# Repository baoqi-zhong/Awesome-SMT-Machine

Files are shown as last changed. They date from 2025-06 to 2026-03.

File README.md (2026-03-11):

# :fire: Awesome :fire: SMT Machine


[中文文档](./README_CN.md)

Contributors:
<p float="left">
  
  
</p>

**Awesome SMT Machine** is an open-source Pick and Place machine project that originated from an embedded system course. The project features a fully self-developed software, hardware, and mechanical design.

It utilizes a **CoreXY** architecture for 4-DOF placement and integrates a custom **FOC (Field Oriented Control) closed-loop stepper motor driver** for high-precision and high-response positioning. The system includes a 4.2-inch color touch screen for real-time status monitoring and uses Python-based host software for coordinate file parsing and fully automatic placement.

<p float="left">
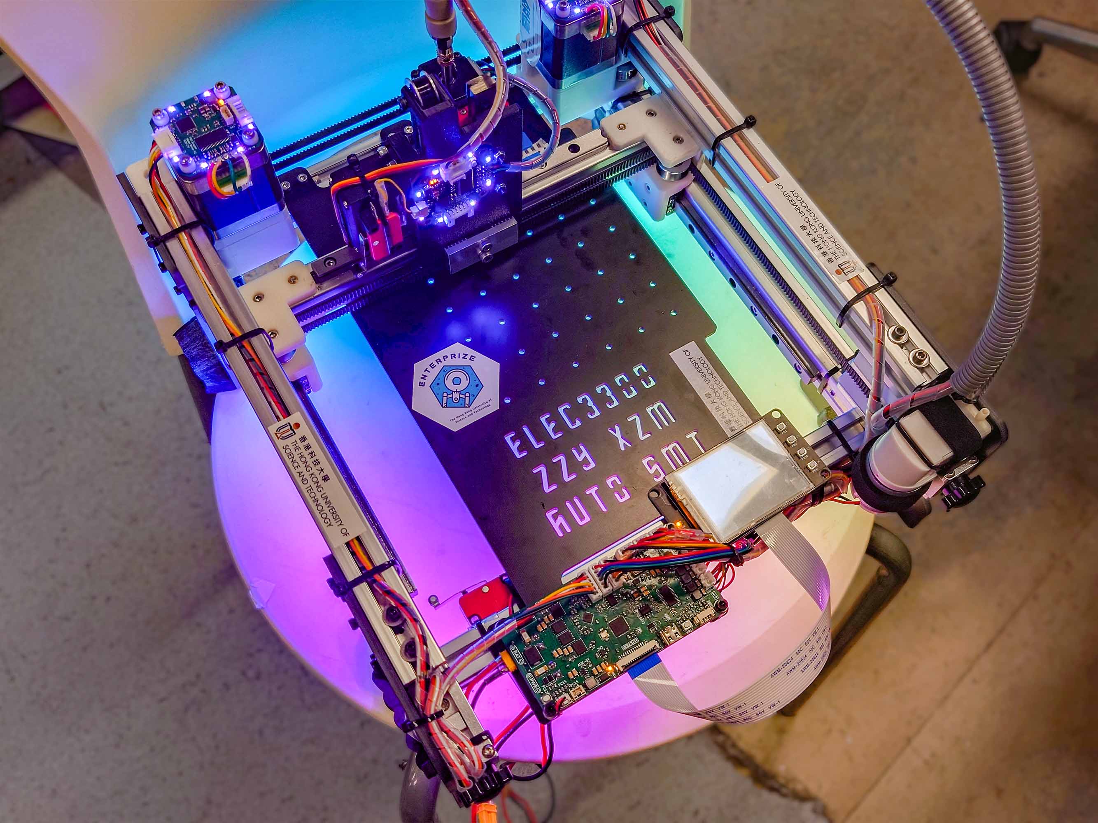
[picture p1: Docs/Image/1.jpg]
  
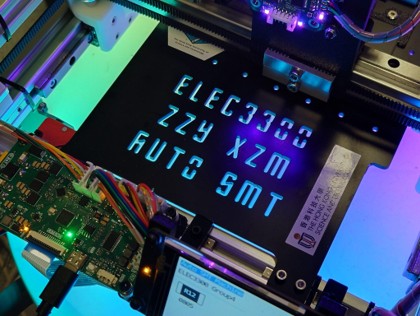
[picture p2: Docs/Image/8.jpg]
  
</p>

**Key Features**:
- **Core-XY Structure**: High precision and high-speed motion.
- **FOC Stepper Driver**: Heat-free, highly efficient, and silent operation.
- **Interactive UI**: 4.2-inch color touch screen.
- **Host Software**: Python-based control for automated workflow.

# Hardware
<p float="left">
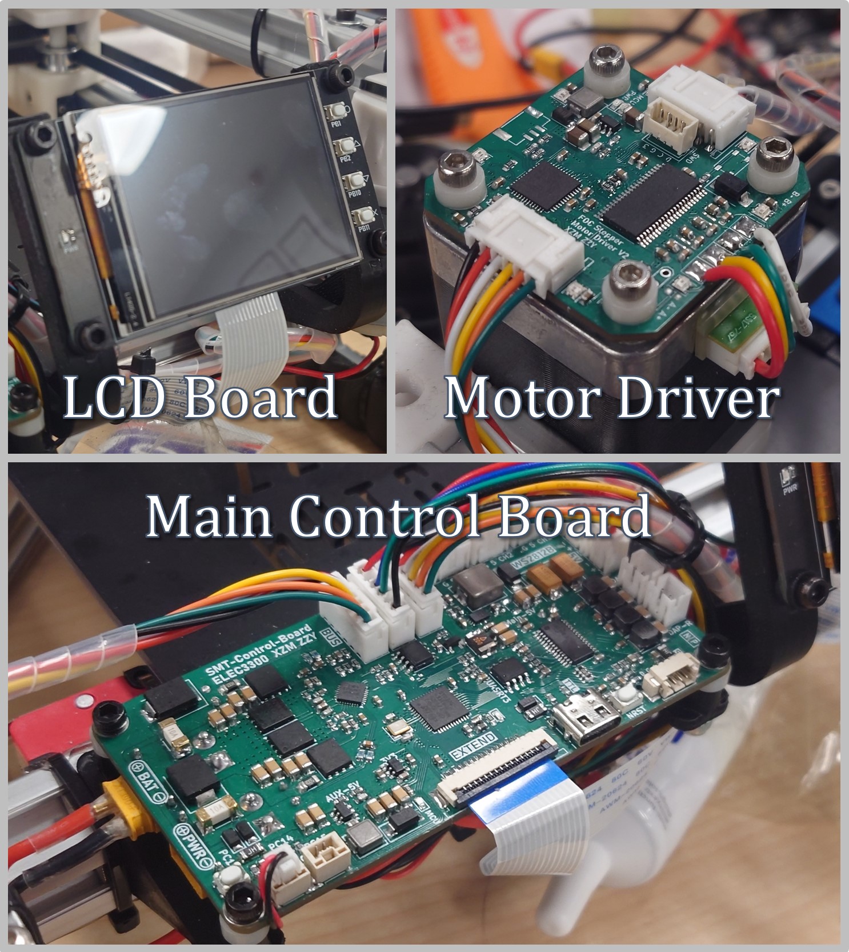
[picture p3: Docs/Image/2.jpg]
  
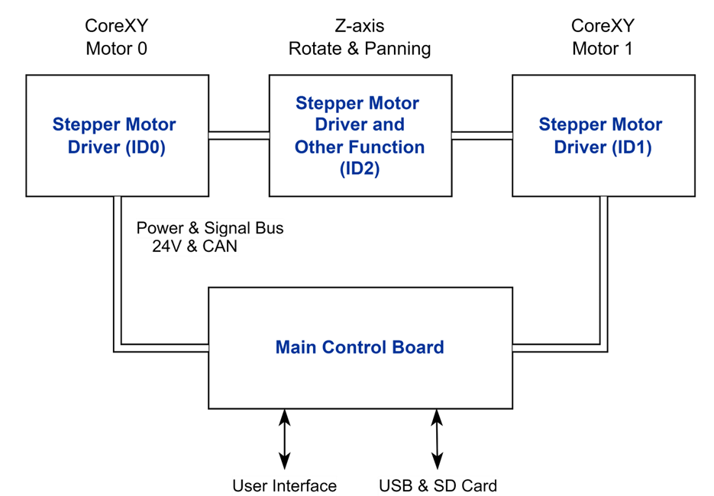
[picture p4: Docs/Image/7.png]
  
</p>

The hardware consists of 4-layer PCBs designed using **KiCad**.

**Directory Structure**:
```
./Hardware/
    Main-Control-Board          Main control motherboard
    Stepper-Motor-FOC-Driver    FOC driver for Nema-17 stepper motors
    LCD-Board                   TFT display interface board
    Dual-Head-Motor-Driver      (Ongoing) Controller for the dual-head placement module
```

## Main Control Board
<p float="left">
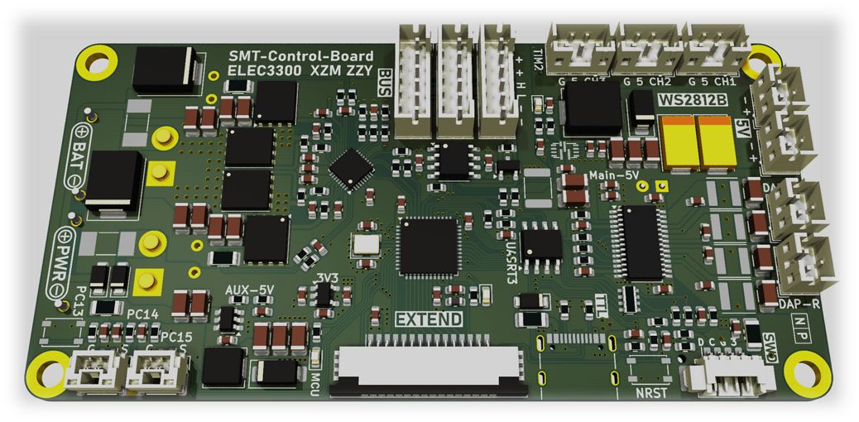
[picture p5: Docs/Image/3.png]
  
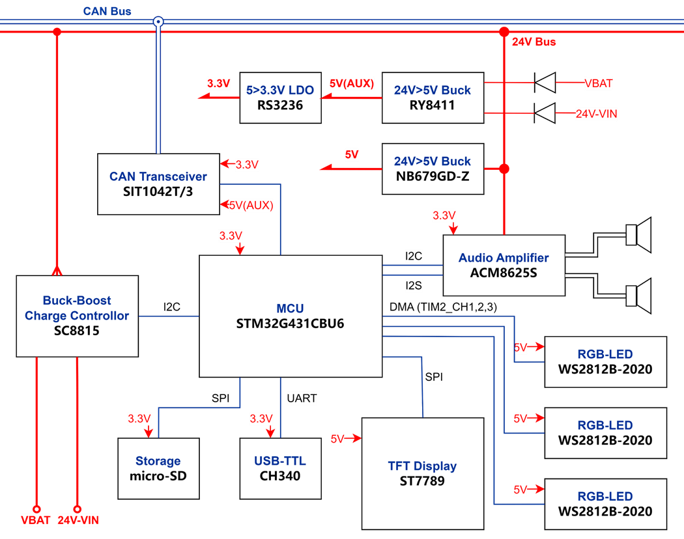
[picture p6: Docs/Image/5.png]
  
</p>

Powered by an **STM32G431CBU6** MCU, SC8815 battery management system, and ACM8625S I2S audio amplifier.  
For details, see [Main Control Board Schematic](./Hardware/Main-Control-Board/Main-Control-Board-Schematic.pdf).

**Features**:
- **UART Interface**: Communication with the Python host software.
- **6S Battery Charger**: Supports fast charging and wide input voltage range.
- **Audio System**: Integrated amplifier and speaker (just for fun! :yum:).
- **CAN Bus**: High reliability and scalability.

## Stepper Motor FOC Driver
<p float="left">
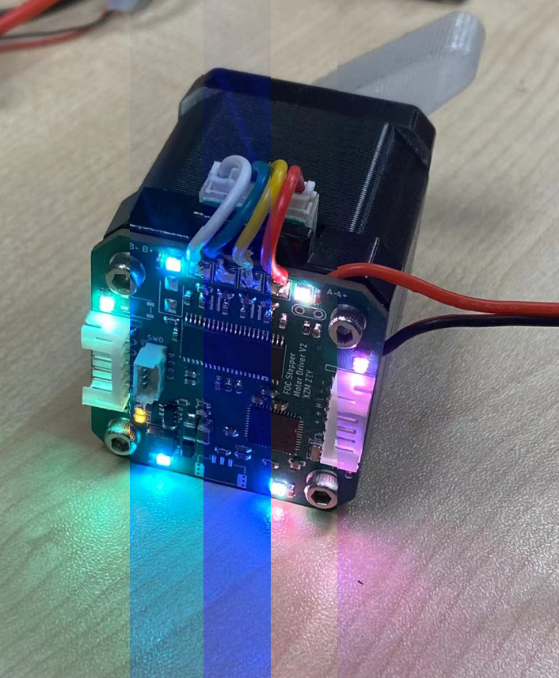
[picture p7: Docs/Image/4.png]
  
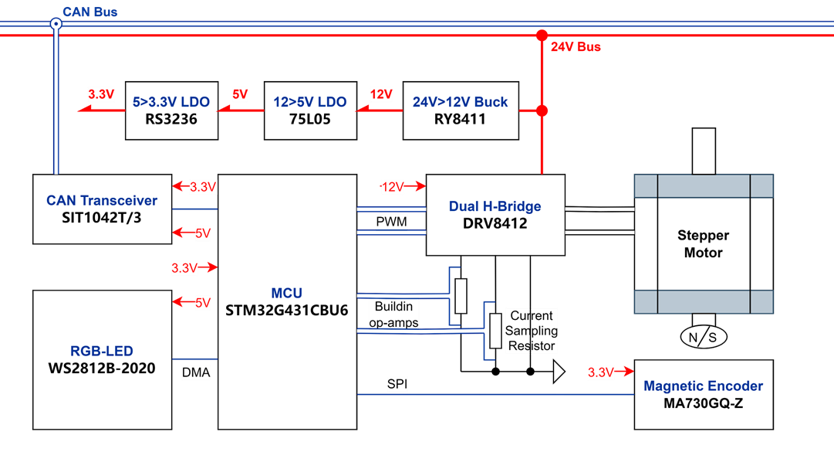
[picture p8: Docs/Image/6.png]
  
</p>

Based on **STM32G431CBU6** MCU, DRV8412 gate driver, MA732 magnetic encoder, and WS2812 RGB LEDs.  
For details, see [Stepper Motor FOC Driver Schematic](./Hardware/Stepper-Motor-FOC-Driver/Stepper-Motor-FOC-Driver-Schematic.pdf).

**Features**:
- **Custom FOC Algorithm**: Three-loop control (Torque, Speed, Angle). Implements DQ-axis decoupling, BEMF feedforward, cogging torque compensation, and dead-time compensation.
- **Precision Control**: Real current loop ensures precise torque control.
- **14-Bit Encoder**: High-speed magnetic encoder with automatic calibration and adaptive notch filter (ANF) for low noise.
- **CAN Bus**: Bi-directional communication.

# Software
The embedded software is developed using **STM32CubeMX**, **Makefile**, and **GCC**. The FOC algorithm is implemented with a bare-metal interrupt-driven architecture for maximum performance. The main control board utilizes **FreeRTOS** for multitasking (communication, motion control, battery management, audio playback, etc.).

**Directory Structure**:
```
./Software/
    ClosePnP                        Python/tkinter-based host control software (inspired by OpenPnP)
    Main-Control-Board-Software     STM32 firmware for the main board
    Stepper-Motor-Driver-Software   FOC algorithm source code
    MusicConverter                  Python script to convert .WAV files to C arrays for audio testing
    Dual-Head-Motor-Driver-Software (Ongoing) Firmware for the dual-head motor driver
```

# Mechanical
The original single-head version was designed using **Cinema 4D (C4D)**. The newer dual-head version is designed with **SolidWorks**.

- **Single-head source files**: `./Mechanical/CoreXY.c4d` (or `./Mechanical/CoreXY.stl`).

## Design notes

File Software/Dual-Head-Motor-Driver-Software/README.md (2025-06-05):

# Dual-Head-Motor-Driver

与电机 FOC 驱动一脉相承. 

## 板上资源
- 三个步进电机的三个全桥驱动
- 三个电机 A 相电流采样(AB 相不共用对地电阻), 以及内部 PGA 运放
- 电机驱动 nFAULT 状态输出
- 输入电压采样
- FDCAN
- GPIO 控制的阀

## TIM 和 ADC: 驱动波形产生与电流采样时机
我们有三个电机, 一共 12 个 timer channel 需要控制, 我们希望他们全部中心对齐. 全部采用中心对齐模式.
对应关系如下:
|相线|Timer & Channel|
|:--|:--|
|M1 A+|TIM3_CH1|
|M1 A-|TIM1_CH1|
|M1 B+|TIM1_CH2|
|M1 B-|TIM1_CH3|
|M2 A+|TIM2_CH1|
|M2 A-|TIM8_CH1N|
|M2 B+|TIM8_CH2N|
|M2 B-|TIM2_CH2|
|M3 A+|TIM4_CH1|
|M3 A-|TIM4_CH2|
|M3 B+|TIM4_CH4|
|M3 B-|TIM4_CH3|

时钟以 timer 1 为准, timer 1 触发 ADC 采样.

```mermaid
graph LR
A("APB1 CLK") --"Prescaler"--> B("TIM1 CLK") --"ARR"--> C("上溢下溢事件") --"Repetition Counter"--> UE("Update Event")-->D("ADC 1 采样") --"DMA Continous Request"--> E("DMA 转换") 
D --"End Of Conversion"--> F("电流环数据处理")
```

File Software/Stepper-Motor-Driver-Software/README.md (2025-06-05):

# RM2025-FOC-Algorithm
General FOC algorithm for BLDC and stepper motor

[TOC]

## 三相 BLDC 驱动波形
### SPWM
我们观察电机反电动势:
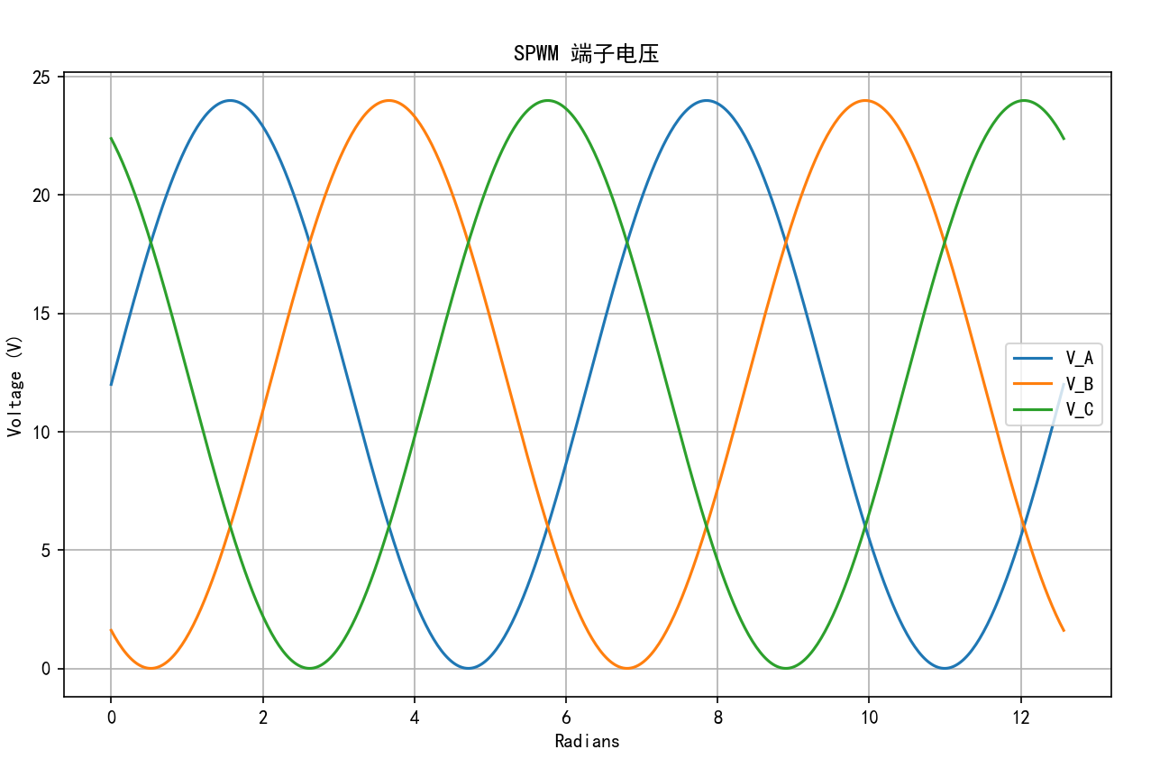
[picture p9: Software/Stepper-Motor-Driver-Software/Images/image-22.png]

> 三个波形分别是三相端子相对三相交汇的中性点 N 点的电势

如果我们在三相端子处产生上图的波形, 则这种调制方式被称为 SPWM. (Sin PWM).

端子电压如下:
\[
\begin{cases}
    V_A = 12\sin(\omega t) + 12 \\
    V_B = 12\sin(\omega t + \frac{2\pi}{3}) + 12 \\
    V_C = 12\sin(\omega t + \frac{4\pi}{3}) + 12 \\
\end{cases}
\]

如果端子电压的范围是 $[0V, 24V]$, 则可计算三相交汇的中性点 $N$ 点的电压:
\[
V_{AN} + V_{BN} + V_{CN} = 0 \\
\therefore V_A + V_B + V_C -3 V_N = 0 \\
\therefore V_N = \frac{1}{3}((12\sin(\omega t) + 12) +  \\
(12\sin(\omega t + \frac{2\pi}{3}) + 12) +  \\
(12\sin(\omega t + \frac{4\pi}{3}) + 12)) = 12V
\]

所以中性点的电压恒为 $12V$, 所以电压的范围是 $[-12V, 12V]$
所以在任意时刻, 3 相电压的大小是:
\[
\begin{cases}
    V_A = 12\sin(\omega t) \\
    V_B = 12\sin(\omega t + \frac{2\pi}{3}) \\
    V_C = 12\sin(\omega t + \frac{4\pi}{3}) \\
\end{cases}
\]
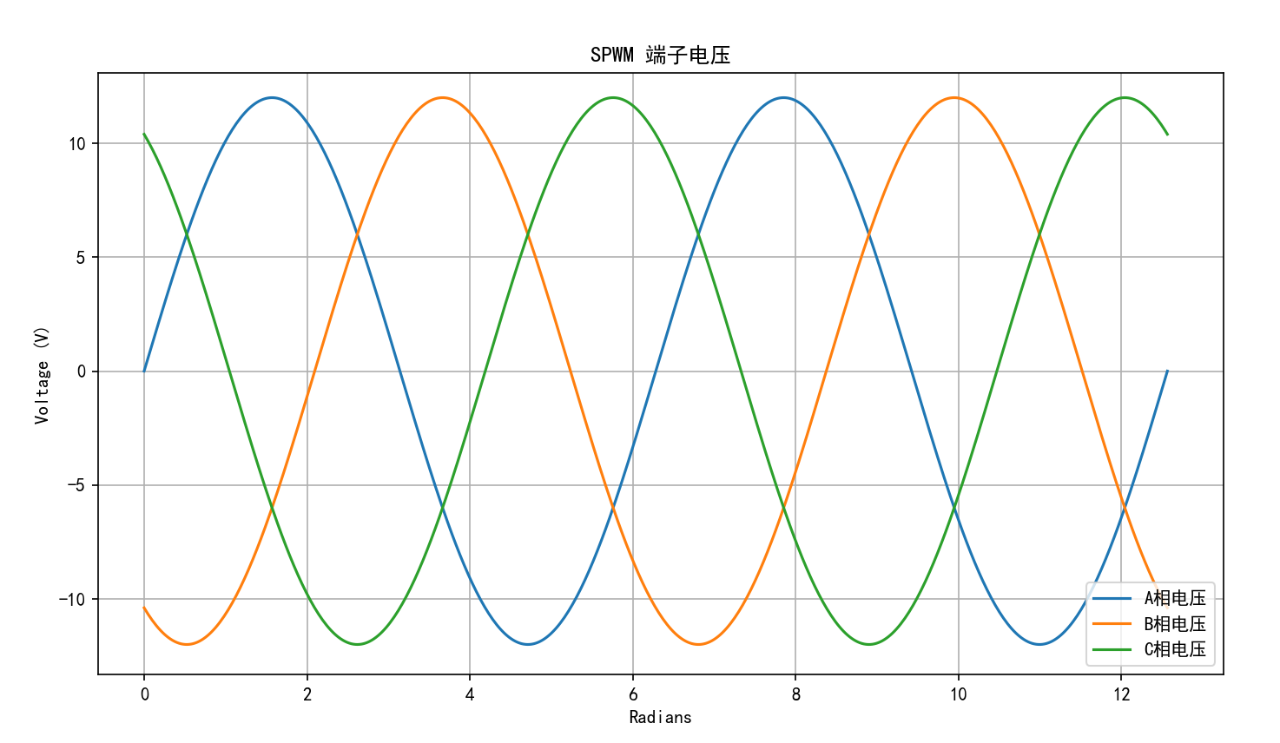
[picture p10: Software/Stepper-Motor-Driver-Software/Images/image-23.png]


3 相电压的矢量和大小是 $12V*2*\frac{\sqrt{3}}{2}\sin(\frac{2\pi}{3}) = 12V*\frac{3}{2} = 18V$

### SVPWM
> 参考资料: [SVPWM算法原理及详解](https://blog.csdn.net/qq_41610710/article/details/120512746)

我们规定 A 相朝右, B 左上, C 右下.

首先, 我们考虑我们能产生多少种基本矢量. 对于三相端子, 每一个都可以是 1 或者 0. 则一共有 8 种基本矢量, 包含两种全 1 全 0 的零矢量. 基本方向矢量互成 60 度角. 如下图:
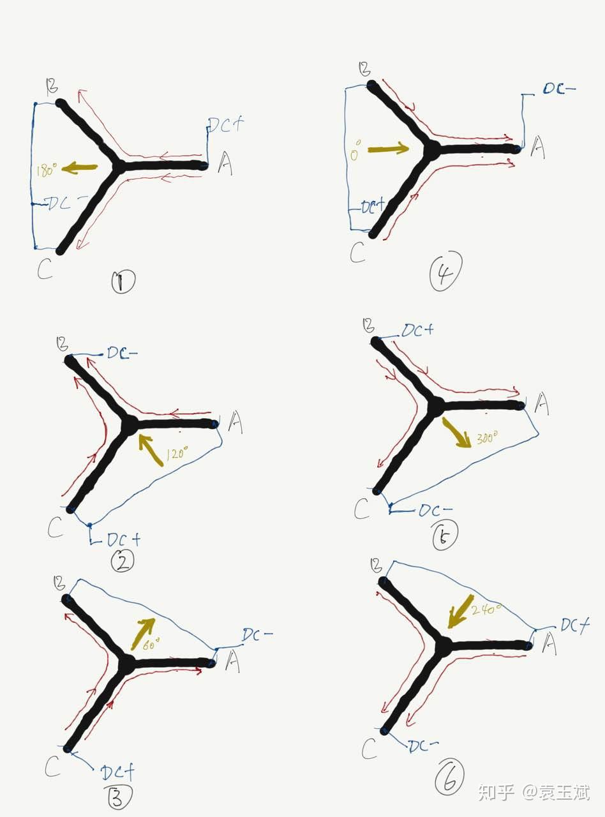
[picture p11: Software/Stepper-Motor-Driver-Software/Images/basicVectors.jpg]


每个基本方向矢量对应三个端子的电平如下:
|矢量|A端子|B端子|C端子|
|:--|:--|:--|:--|
|$U_4$|1|0|0|
|$U_6$|1|1|0|
|$U_2$|0|1|0|
|$U_3$|0|1|1|
|$U_1$|0|0|1|
|$U_5$|1|0|1|

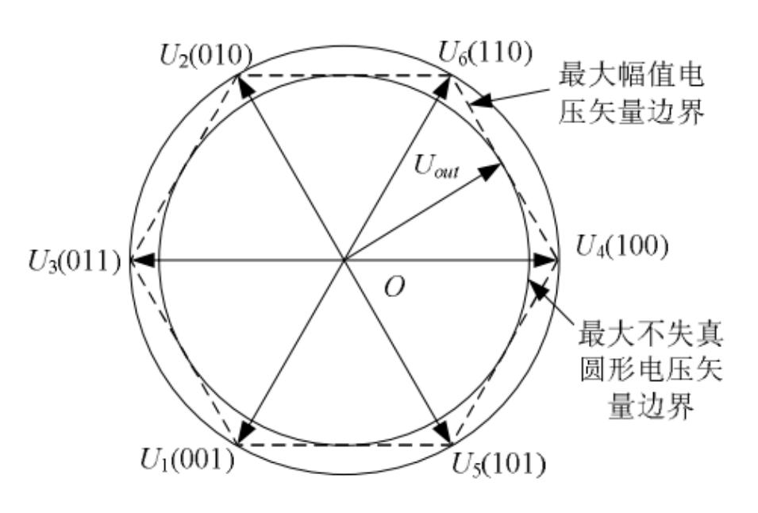
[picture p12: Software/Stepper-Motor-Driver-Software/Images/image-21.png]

下面我们分析电压矢量的大小. 
> 参考资料: [SVPWM之矢量幅值](https://jianwei.fun/?p=2037)

**基本方向矢量**: 以 $U_4$ 为例, 输出 $U_A = 24V$, $U_B = 0V$, $U_C = 0V$, 此时三个相线圈构成分压电路: $A$ 相电压为 $24V * \frac{2}{3} = 16V$; $B, C$ 相电压为 $24V * \frac{1}{3} = 8V$. 所以对于 $U_4$ 等效相电压的矢量大小是 $16 + 2*8*\frac{1}{2}=24V$. 所以对于 6 个基本方向的矢量, 最大电压边界为 $24V$.
**任意方向矢量**: 由于最大导通时间是固定的, 所以任意角度的最大幅值电压矢量的边界是基本方向矢量的 Liner Combination, 也就是图中的 **六边形**.
**不过调制任意方向矢量**: 但是我们希望最大电压的大小是均匀的, 所以我们取六边形的内接圆. 所以 3 相电压的矢量和大小是 $24 * \frac{\sqrt{3}}{2} = 12\sqrt{3} V$

我们对比发现, SVPWM 能产生的相电压的矢量和的大小是 SPWM 的 $\frac{2}{\sqrt{3}} = 1.15$ 倍, 电压利用率高了 $15\%$

**SVPWM 波形生成**
我们的目标是写一个函数能输出特定方向特定大小的电压矢量. (其实我们更加希望得到的是, 给定 $Uq, Ud, angle$ 输出三相 PWM 的占空比)
我们使用 uint16_t 定点数表示角度. 我们首先判断目标角度所在的扇区, 然后生成对应波形.

我们首先进行反 Park 变换, 把 $U_q, U_d$ 转换为 $U_{alpha}, U_{beta}$. 然后进行反 Clark 变换, 得到相邻基本矢量的作用时长. 最后根据扇区设计 7 段式 PWM 构造占空比.
在进行 反 Park 变换 的时候, 我们需要保证 $U_{alpha}^2 + U_{beta}^2 <= 1$ 我们可以对 $U_q, U_d$ 进行缩放, 也可以对 $U_{alpha}, U_{beta}$ 进行缩放. 在这里, 我们选择对 $U_{alpha}, U_{beta}$ 进行缩放.
很显然, 如果 $U_{alpha}^2 + U_{beta}^2 > 1$ 那么缩放的比例 ratio 为 $\frac{1}{\sqrt{U_{alpha}^2 + U_{beta}^2}}$. 我们可以用个快速平方根倒数算法玩一下.

**扇区判断**
> 参考资料: [SVPWM扇区判断](https://jianwei.fun/?p=2113)

根据目标坐标在划分平面的 6 条直线上下方进行判断.
\[
\begin{cases}
    l_1: y=0 \\
    l_2: y=\sqrt{3}x \\
    l_3: y=-\sqrt{3}x
\end{cases}
\]

**计算相邻基本矢量的作用时长**
> 参考资料: [SVPWM相邻矢量作用时长计算](https://jianwei.fun/?p=2140)

需要注意的是, 我们不希望在 $U_{alpha} = 1, U_{beta} = 0$ 的时候算出 $X = 1, Y = 0$, 而是希望算出 $X = \frac{\sqrt{3}}{2}, Y = 0$ 因为即使我们有能力产生大小为 1 的电压矢量, 我们需要保证全程都在六边形里面, 所以根据上文我们选择六边形的内接圆, 所以我们整体乘上 $\frac{\sqrt{3}}{2}$

1. **第一象限**
\[
\frac{2}{\sqrt{3}}
\begin{bmatrix}
    1 & \frac{1}{2} \\
    0 & \frac{\sqrt{3}}{2} \\
\end{bmatrix}
\begin{bmatrix}
    X \\
    Y \\
\end{bmatrix} =
\begin{bmatrix}
    U_{alpha} \\
    U_{beta} \\
\end{bmatrix}
\]
计算逆矩阵
\[
\frac{\sqrt{3}}{2}
\begin{bmatrix}
    1 & -\frac{1}{\sqrt{3}} \\
    0 & \frac{2}{\sqrt{3}} \\
\end{bmatrix}
\begin{bmatrix}
    U_{alpha} \\
    U_{beta} \\
\end{bmatrix} =
\begin{bmatrix}
    X \\
    Y \\
\end{bmatrix}
\]

2. **第二象限**
\[
\frac{2}{\sqrt{3}}
\begin{bmatrix}
    \frac{1}{2} & -\frac{1}{2}\\
    \frac{\sqrt{3}}{2} & \frac{\sqrt{3}}{2} \\
\end{bmatrix}
\begin{bmatrix}
    X \\
    Y \\
\end{bmatrix} =
\begin{bmatrix}
    U_{alpha} \\
    U_{beta} \\
\end{bmatrix}
\]
计算逆矩阵
\[
\frac{\sqrt{3}}{2}
\begin{bmatrix}
    1 & \frac{1}{\sqrt{3}} \\
    -1 & \frac{1}{\sqrt{3}} \\
\end{bmatrix}
\begin{bmatrix}
    U_{alpha} \\
    U_{beta} \\
\end{bmatrix} =
\begin{bmatrix}
    X \\
    Y \\
\end{bmatrix}
\]

3. **第三象限**
\[
\frac{2}{\sqrt{3}}
\begin{bmatrix}
    -\frac{1}{2} & -1 \\
    \frac{\sqrt{3}}{2} & 0 \\
\end{bmatrix}
\begin{bmatrix}
    X \\
    Y \\
\end{bmatrix} =
\begin{bmatrix}
    U_{alpha} \\
    U_{beta} \\
\end{bmatrix}
\]
计算逆矩阵
\[
\frac{\sqrt{3}}{2}
\begin{bmatrix}
    0 & \frac{2}{\sqrt{3}} \\
    -1 & -\frac{1}{\sqrt{3}} \\
\end{bmatrix}
\begin{bmatrix}
    U_{alpha} \\
    U_{beta} \\
\end{bmatrix} =
\begin{bmatrix}
    X \\
    Y \\
\end{bmatrix}
\]

4. **第四象限**
\[
\frac{2}{\sqrt{3}}
\begin{bmatrix}
    -1 & -\frac{1}{2}\\
    0 & -\frac{\sqrt{3}}{2} \\
\end{bmatrix}
\begin{bmatrix}
    X \\
    Y \\
\end{bmatrix} =
\begin{bmatrix}
    U_{alpha} \\
    U_{beta} \\
\end{bmatrix}
\]
计算逆矩阵
\[
\frac{\sqrt{3}}{2}
\begin{bmatrix}
    -1 & \frac{1}{\sqrt{3}} \\
    0 & -\frac{2}{\sqrt{3}} \\
\end{bmatrix}
\begin{bmatrix}
    U_{alpha} \\
    U_{beta} \\
\end{bmatrix} =
\begin{bmatrix}
    X \\
    Y \\
\end{bmatrix}
\]

5. **第五象限**
\[
\frac{2}{\sqrt{3}}
\begin{bmatrix}
    -\frac{1}{2} & \frac{1}{2}\\
    -\frac{\sqrt{3}}{2} & -\frac{\sqrt{3}}{2} \\
\end{bmatrix}
\begin{bmatrix}
    X \\
    Y \\
\end{bmatrix} =
\begin{bmatrix}
    U_{alpha} \\
    U_{beta} \\
\end{bmatrix}
\]
计算逆矩阵
\[
\frac{\sqrt{3}}{2}
\begin{bmatrix}
    -1 & -\frac{1}{\sqrt{3}} \\
    1 & -\frac{1}{\sqrt{3}} \\
\end{bmatrix}
\begin{bmatrix}
    U_{alpha} \\
    U_{beta} \\
\end{bmatrix} =
\begin{bmatrix}
    X \\
    Y \\
\end{bmatrix}
\]

6. **第六象限**
\[
\frac{2}{\sqrt{3}}
\begin{bmatrix}
    \frac{1}{2} & 1 \\
    -\frac{\sqrt{3}}{2} & 0 \\
\end{bmatrix}
\begin{bmatrix}
    X \\
    Y \\
\end{bmatrix} =
\begin{bmatrix}
    U_{alpha} \\
    U_{beta} \\
\end{bmatrix}
\]
计算逆矩阵
\[
\frac{\sqrt{3}}{2}
\begin{bmatrix}
    0 & -\frac{2}{\sqrt{3}} \\
    1 & \frac{1}{\sqrt{3}} \\
\end{bmatrix}
\begin{bmatrix}
    U_{alpha} \\
    U_{beta} \\
\end{bmatrix} =
\begin{bmatrix}
    X \\
    Y \\
\end{bmatrix}
\]

---

计算出每个象限的 X Y 分量之后, 我们产生 **7 段式 PWM**. **7 段式 PWM** 的思想是每次只切换一个 MOS 管的开关状态, 以中心对称的形式产生 PWM 波形, 这样可以尽可能地减少谐波, 保留基波能量.
每一个象限都会用到 $U_0, U_7$ 两个零矢量来补足时间.

需要注意的是, 产生 SVPWM 的顺序总是从 $U_0$ 开始 $U_7$ 结束, 且两个基本矢量要按从小到大排序.

1. **第一象限**
$U_4, U_6, U_0, U_7$

```wavedrom
{"signal": [
    {"name": "A 端子", "wave": "01.....0"},
    {"name": "B 端子", "wave": "0.1...0."},
    {"name": "C 端子", "wave": "0..1.0.."},
    {"name": "电压矢量", "wave": "23422432", "data": ["U0", "U4", "U6", "U7", "U7", "U6", "U4", "U0"] }
]}
```
$T_X = U_4; T_Y = U_6$

$\therefore T_C = \frac{1 - T_X - T_Y}{2}$
$T_B = T_C + T_Y$
$T_A = T_B + T_X$

\[
\therefore 
\begin{cases}
    T_A = \frac{1 + T_X + T_Y}{2} \\
    T_B = \frac{1 - T_X + T_Y}{2} \\
    T_C = \frac{1 - T_X - T_Y}{2} \\
\end{cases}
\]

2. **第二象限**
$U_2, U_6, U_0, U_7$

```wavedrom
{"signal": [
    {"name": "A 端子", "wave": "0.1...0."},
    {"name": "B 端子", "wave": "01.....0"},
    {"name": "C 端子", "wave": "0..1.0.."},
    {"name": "电压矢量", "wave": "23422432", "data": ["U0", "U2", "U6", "U7", "U7", "U6", "U2", "U0"] }
]}
```

$T_X = U_6; T_Y = U_2$

$\therefore T_C = \frac{1 - T_X - T_Y}{2}$
$T_A = T_C + T_X$
$T_B = T_A + T_Y$

\[
\therefore 
\begin{cases}
    T_A = \frac{1 + T_X - T_Y}{2} \\
    T_B = \frac{1 + T_X + T_Y}{2} \\
    T_C = \frac{1 - T_X - T_Y}{2} \\
\end{cases}
\]

3. **第三象限**
$U_2, U_3, U_0, U_7$

```wavedrom
{"signal": [
    {"name": "A 端子", "wave": "0..1.0.."},
    {"name": "B 端子", "wave": "01.....0"},
    {"name": "C 端子", "wave": "0.1...0."},
    {"name": "电压矢量", "wave": "23422432", "data": ["U0", "U2", "U3", "U7", "U7", "U3", "U2", "U0"] }
]}
```

$T_X = U_2; T_Y = U_3$

$\therefore T_A = \frac{1 - T_X - T_Y}{2}$
$T_C = T_A + T_Y$
$T_B = T_C + T_X$

\[
\therefore 
\begin{cases}
    T_A = \frac{1 - T_X - T_Y}{2} \\
    T_B = \frac{1 + T_X + T_Y}{2} \\
    T_C = \frac{1 - T_X + T_Y}{2} \\
\end{cases}
\]

4. **第四象限**
$U_1, U_3, U_0, U_7$

```wavedrom
{"signal": [
    {"name": "A 端子", "wave": "0..1.0.."},
    {"name": "B 端子", "wave": "0.1...0."},
    {"name": "C 端子", "wave": "01.....0"},
    {"name": "电压矢量", "wave": "23422432", "data": ["U0", "U1", "U3", "U7", "U7", "U3", "U1", "U0"] }
]}
```

$T_X = U_3; T_Y = U_1$

$\therefore T_A = \frac{1 - T_X - T_Y}{2}$
$T_B = T_A + T_X$
$T_C = T_B + T_Y$

\[
\therefore 
\begin{cases}
    T_A = \frac{1 - T_X - T_Y}{2} \\
    T_B = \frac{1 + T_X - T_Y}{2} \\
    T_C = \frac{1 + T_X + T_Y}{2} \\
\end{cases}
\]

5. **第五象限**
$U_1, U_5, U_0, U_7$

```wavedrom
{"signal": [
    {"name": "A 端子", "wave": "0.1...0."},
    {"name": "B 端子", "wave": "0..1.0.."},
    {"name": "C 端子", "wave": "01.....0"},
    {"name": "电压矢量", "wave": "23422432", "data": ["U0", "U1", "U5", "U7", "U7", "U5", "U1", "U0"] }
]}
```

$T_X = U_1; T_Y = U_5$

$\therefore T_B = \frac{1 - T_X - T_Y}{2}$
$T_A = T_B + T_Y$
$T_C = T_A + T_X$

\[
\therefore 
\begin{cases}
    T_A = \frac{1 - T_X + T_Y}{2} \\
    T_B = \frac{1 - T_X - T_Y}{2} \\
    T_C = \frac{1 + T_X + T_Y}{2} \\
\end{cases}
\]

6. **第六象限**
$U_4, U_5, U_0, U_7$

```wavedrom
{"signal": [
    {"name": "A 端子", "wave": "01.....0"},
    {"name": "B 端子", "wave": "0..1.0.."},
    {"name": "C 端子", "wave": "0.1...0."},
    {"name": "电压矢量", "wave": "23422432", "data": ["U0", "U4", "U5", "U7", "U7", "U5", "U4", "U0"] }
]}
```

$T_X = U_5; T_Y = U_4$

$\therefore T_B = \frac{1 - T_X - T_Y}{2}$
$T_C = T_B + T_X$
$T_A = T_C + T_Y$

\[
\therefore 
\begin{cases}
    T_A = \frac{1 + T_X + T_Y}{2} \\
    T_B = \frac{1 - T_X - T_Y}{2} \\
    T_C = \frac{1 + T_X - T_Y}{2} \\
\end{cases}
\]

至此, SVPWM 解算完毕.

需要注意的是, 代码里 outputUq 控制的是总相电压的矢量和大小, 而不是单独一相的电压大小

### 谐波注入
> 参考资料: [SPWM中三次谐波注入幅值的确定](https://blog.csdn.net/qq_50632468/article/details/116561097)

我们关心的是相电压, 是真正产生扭矩电流的电压. 如果我们给三相的端子电压同时加减一个共模电压, 相电压是不会改变的.
一种操作是, **三次谐波注入**. 意思是往三相同时加入频率为基波三倍的波形(三次谐波). 注入了三次谐波之后, 端子电压如下:
\[
\begin{cases}
    V_A = 12\sin(\omega t) + 12 + 12\cdot\frac{1}{6}\sin(3\omega t)\\
    V_B = 12\sin(\omega t + \frac{2\pi}{3}) + 12 + 12\cdot\frac{1}{6}\sin(3\omega t)\\
    V_C = 12\sin(\omega t + \frac{4\pi}{3}) + 12 + 12\cdot\frac{1}{6}\sin(3\omega t)\\
\end{cases}
\]
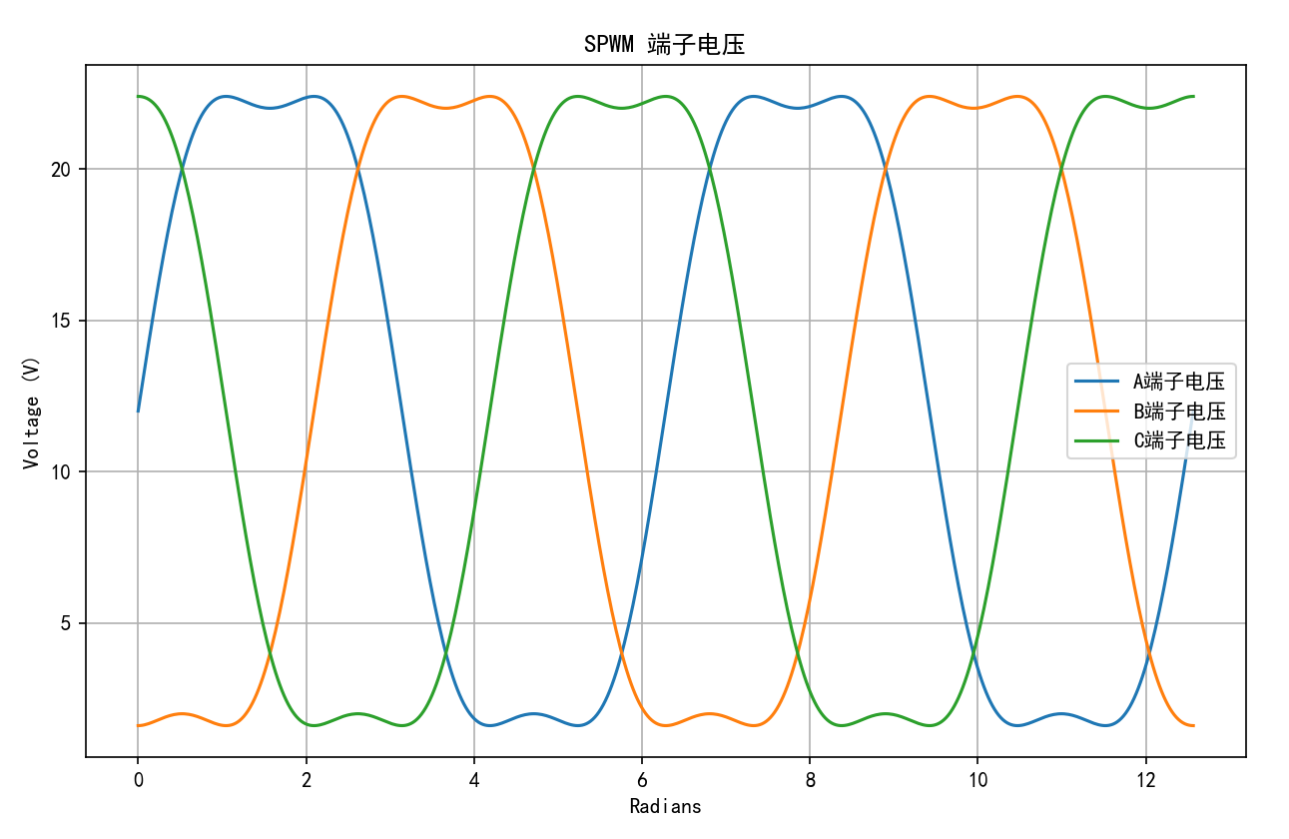
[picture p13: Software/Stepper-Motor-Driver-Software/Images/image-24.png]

我们发现, 在注入三次谐波之后, 端子电压的 Peak-to-peak 电压减小了. 经计算, 端子电压的 Peak-to-peak 减小为 $24V * \frac{\sqrt{3}}{2} = 20.78456V$. 因此, 我们可以对调制电压进行缩放, 缩放为原来的 $\frac{2}{\sqrt{3}} = 1.15$ 倍. 
因为我们是对三个端子的电压同时加上了一个共模电压, 所以相电压也变为原来的 $1.15$ 倍.

我们可以计算三相交汇的中性点 $N$ 点的电压:
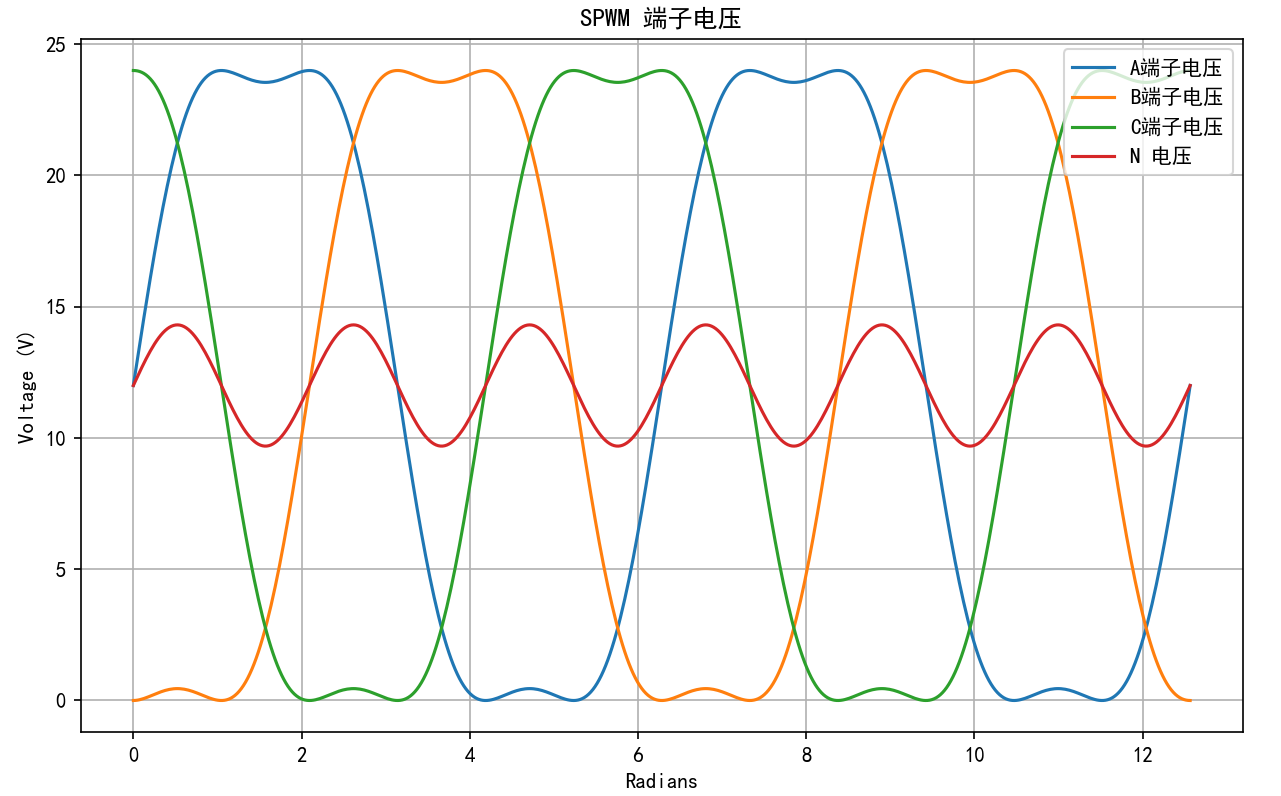
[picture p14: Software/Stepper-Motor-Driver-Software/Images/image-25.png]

可以看到, 中性点 $N$ 点的电压正是我们注入进去的三次谐波.

---

**谐波注入与 SVPWM 区别**
我们可以画出 SVPWM 三相端子的电压曲线: \[TODO\]

## 两相步进电机 SVPWM ?
我们规定硬件连接:
htim1 CN1: A+
htim1 CN2: A-
htim1 CN3: B+
htim1 CN4: B-
规定以 A 为 alpha 轴, B 为 beta 轴.
在三相无刷电机控制中, 三个 PWM 通道实际上只有两个自由度, 因为需要满足电流和为 0. 所以, 我们需要进行 Clark 变换, 把三相电流矢量从 abc 坐标系降为到 Alpha Beta 坐标系方便控制.

但是我们注意到, 在两相步进电机中, 不存在两相电流的约束关系, 同时 A 相的开关对 B 相电流采样没有影响. 所以我们并不需要使用 SVPWM 对步进电机进行控制, 也不需要进行 Clark 变换, 因为步进电机的线圈轴直接就相当于 Alpha Beta 轴. 所以我们可以 **直接** 给两个通道的 CCR 寄存器赋值来控制电流.

我们直接通过修改寄存器控制两相四桥的通断情况来控制等效相电压. 对任意一相, 我们维持其中一个半桥**完全关闭**, 然后控制另一半桥的 High Low.
对于线序相反的步进电机, 只需要修改通道对应关系即可.

## TIM 和 ADC: 驱动波形产生与电流采样时机

**为什么需要用中心对齐 PWM**
因为采样电阻放在下管, 如下图:
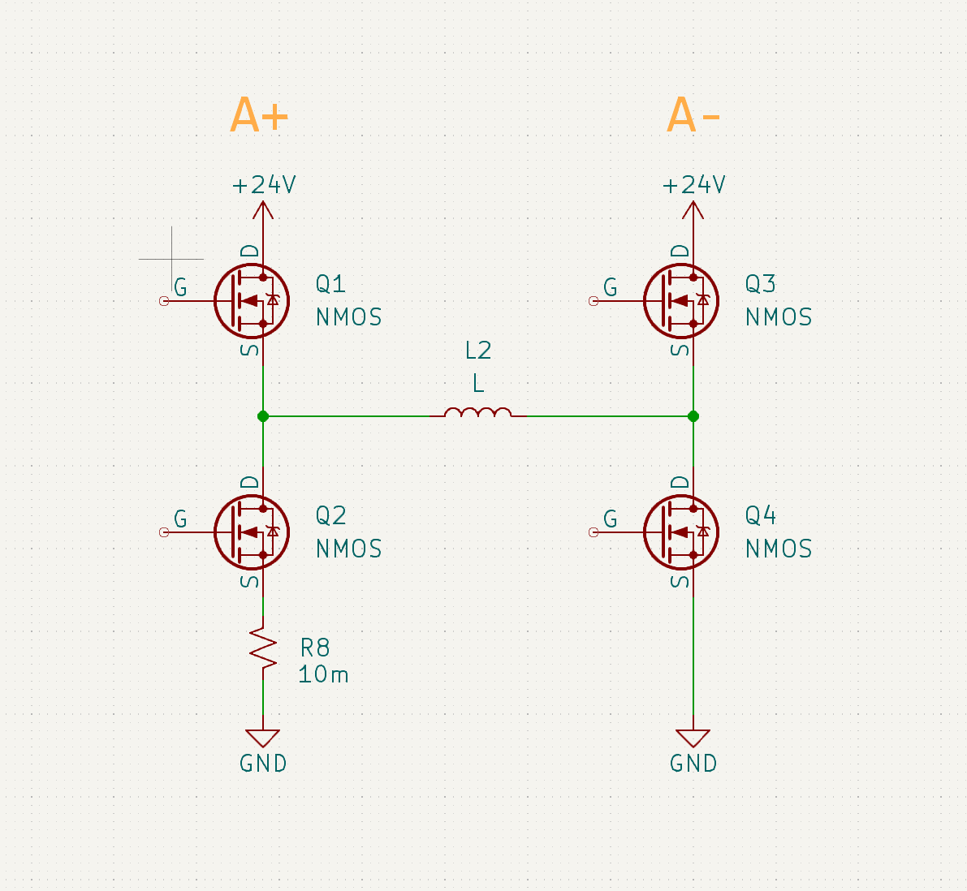
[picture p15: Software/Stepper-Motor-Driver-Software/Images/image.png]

只有在 A 侧下管打开的时候才能对相电流进行采样. 根据相电流方向不同, 分为两张情况:
- 电流从 A- 到 A+ 的时候 A+ 侧下管常开, 可以任意时间采样; 
- 电流从 A+ 到 A- 的时候 A+ 侧产生 PWM 波形, 需要在两个下管同时打开的时候采样, 也就是 PWM1 CN1 和 CN2 同时为 0 的时候触发采样. 

因此, 不管是哪个电流方向, 选择 PWM1 CN1 和 CN2 同时为 0 的时候触发采样能够满足要求. 此外, 我们希望 ADC 采样的间隔距离 PWM 动作点越远越好, 也就是 L->H 和 H->L 的中间最好. 因此, 我们使用 **中心对齐模式** 的 PWM, 然后使用 **Update Event** 触发 ADC 采样:
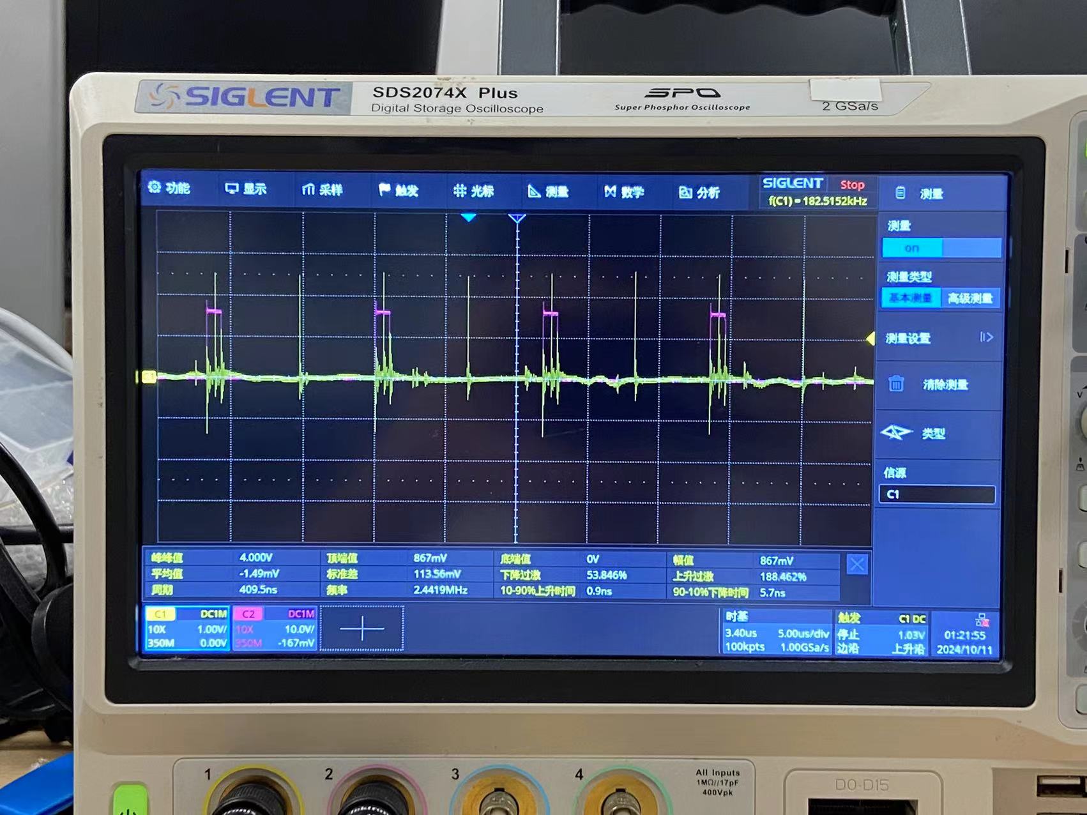
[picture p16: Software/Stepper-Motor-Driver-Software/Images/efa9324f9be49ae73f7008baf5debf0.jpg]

> 红色部分为 TIM1 其中一个 PWM 输出通道的波形, 黄色脉冲信号为 Update Event事件

在 CubeMX 里有个配置叫做 **Repetition Counter**, 它会在产生 (Repetition Counter + 1) 次上溢出之后才真正产生 Update Event 驱动 ADC. 因此, 我们把 Repetition Counter 配置为 1, 我们希望在上图 PWM 为 **LOW** 的最中点进行采样.

存在的一个问题是, 如果直接把 Repetition Counter 配置为 1, 采样会发生在偶数次 Event, 也就是 PWM 为 **HIGH** 的最中点处, 这不是我们希望的. 我们希望跳过第一个 Event, 然后在所有的奇数 Event 上采样.
实现这一点的方法在 Reference Manual RM0440.pdf 的 Figure 289. Update rate examples depending on mode and TIMx_RCR register settings 里, 即在 HAL_TIM_PWM_Start 之前手动 HAL_TIM_Base_Start 然后更新 Repetition Counter 寄存器为 1. 这样这个 1 值就会在下一次 Update Event.
具体代码是:
```c
// 这样做的目的是修改 TIM1 Update Event 的相位
HAL_TIM_Base_Start_IT(&htim1);
htim1.Instance->RCR = 1;

HAL_TIM_PWM_Start(&htim1, TIM_CHANNEL_1);
HAL_TIM_PWM_Start(&htim1, TIM_CHANNEL_2);
HAL_TIM_PWM_Start(&htim1, TIM_CHANNEL_3);
HAL_TIM_PWM_Start(&htim1, TIM_CHANNEL_4);
```

最终, 我们成功过滤出目标 Update Event 如下:
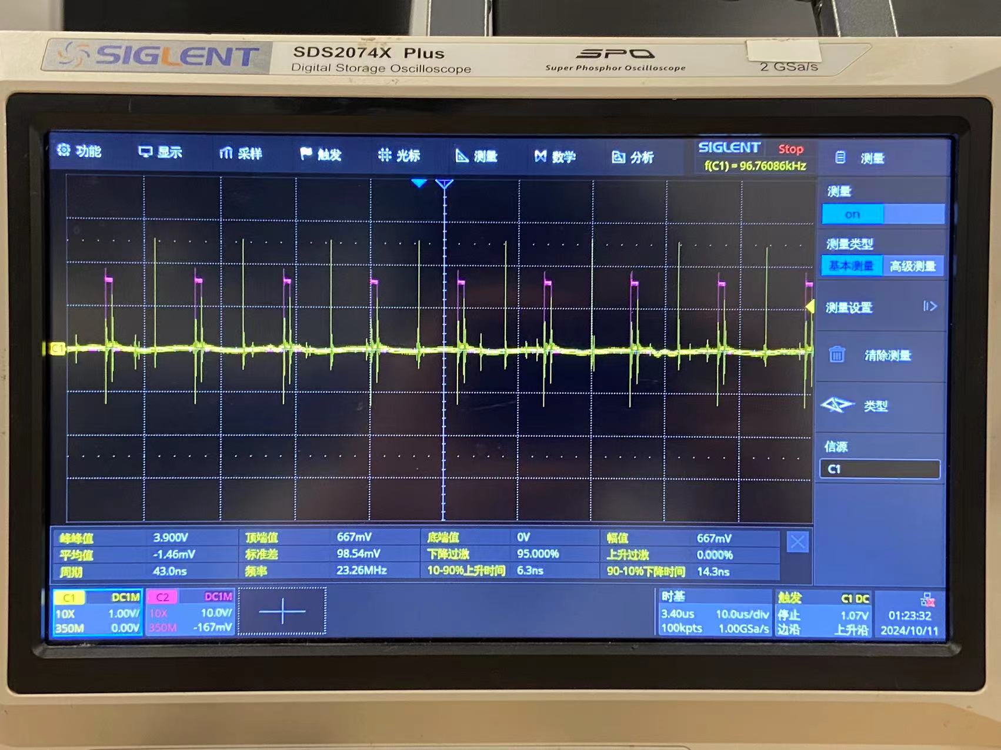
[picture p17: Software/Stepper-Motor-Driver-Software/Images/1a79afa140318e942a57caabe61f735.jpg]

> 红色部分为 TIM1 其中一个 PWM 输出通道的波形, 黄色脉冲信号为 Update Event事件

---
接下来我们进行 **TIM 和 ADC 的 CubeMX 配置**.

1. 配置 TIM 模式为中央对齐模式
这样 TIM 的 counter 会先往上计数直到 ARR, 然后往下计数直到 0.
在计数到 ARR 之后, 会根据 **Repetition Counter** 产生 **Update Event**, 我们在 TIM 配置里把 Trigger Event Selection TRGO 选择为 Update Event 用来触发 ADC

2. 选择 PWM 模式
PWM 模式为 **PWM Mode 1**, 即正常极性. 配置为 High Polarity, 正常极性.

3. 选择 TIM 的 Output Event 为 Update Event, 如上文所述.

4. ADC 配置
在 ADC 里选择触发源为 **Timer 1 Trigger Out  Event**. 接受从 TIM 传来的

打开 DMA, 选择 **Circular Mode**, 同时打开 **DMA Continous Request**. 
**Circular Mode** 说的是如何处理 Buffer, 这里是把 Buffer 视为环形队列, 在软件单次触发或者 DMA Continous Request 触发, 把 buffer 填满了之后, 自动从头覆盖 buffer.
**DMA Continous Request** 是指在 ADC 单个通道转换完成之后自动触发 DMA 请求. 这样能保证多个通道之间的数据不会相互覆盖.

如果有多个通道, 我们打开 **Scan Mode**. Scan Mode 是在软件或者外部触发一次之后, 把所有通道都转换了. 必须配合 DMA + DMA Continous Request 使用, 否则后面的通道会把前面的覆盖掉.

**End Of Conversion** 作用是什么时候产生结束中断, 这里我们配成所有通道都转换完成才产生一次请求. 我们把电流环的程序放在 ADC 采样完成的回调函数里, 这样实现最高频率的电流环闭环.

所以整个调用链是这样的:
```mermaid
graph LR
A("APB1 CLK") --"Prescaler"--> B("TIM1 CLK") --"ARR"--> C("上溢下溢事件") --"Repetition Counter"--> UE("Update Event")-->D("ADC 1 采样") --"DMA Continous Request"--> E("DMA 转换") 
D --"End Of Conversion"--> F("电流环数据处理")
```

## 离散控制
突然想到一个很严重的问题, 就是 CCR = 1000 的话, 控制精度只有不到 10 bit, 相当于最小可控相电压是 24mV, 最小可控相电流是 100mA, 这是不可接受的.
所以结论是, timer 的 prescaler 是邪恶的, 让控制精度降低了, 正确操作应该是在 CCR 范围允许的情况下, 尽可能让 prescaler = 0.

电流环 & PWM 频率: $\frac{170MHz}{2*CCR} = \frac{170MHz}{2*4000} = 21.5KHz$
PWM 分辨率: 4000(12bits)
中心对齐模式的一个不好之处是脉冲宽度只能是偶数, 相当于精度降低了一倍.

## 电流采样与校准
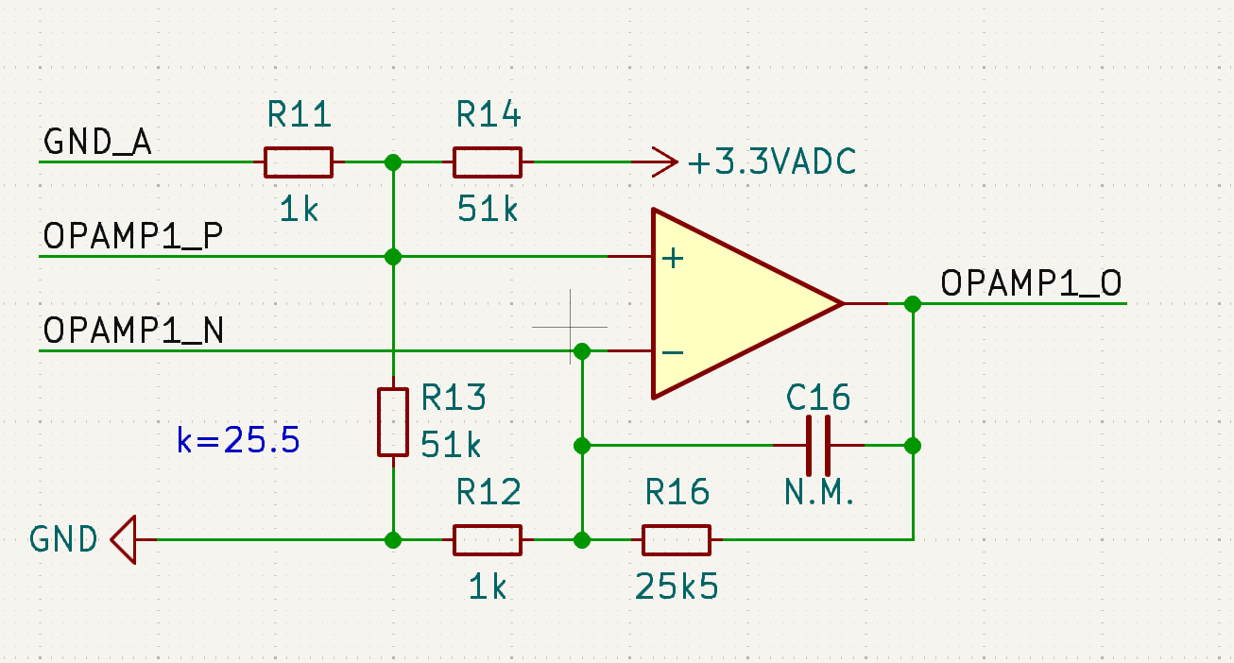
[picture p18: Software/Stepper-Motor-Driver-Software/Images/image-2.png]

使用 G4 内部运放构成同向放大器. 

**双向电流采集** 
由 2400 可知这是个非常经典的同向加法放大器. Opamp 输出电压被施加了 1.65V 偏置, 正反电流采样的范围一样.

**G4 内部运放**
这里选择 **Stand Alone** 模式, G4 内部的运放需要使用 **HAL_OPAMP_START** 来启用, 有点逆天, 老是忘记. 内部运放输出脚接出来, 可以同时使能 ADC 的引脚功能. 所以不属于 internally connect, 而是通过 pin 在外部实现连接.

**双 ADC 同步采样**
上面我们是使用两个 adc 分别进行采样, 使用两个 DMA 分别进行数据搬运. 存在一个可能是, 第一个 ADC 的 DMA 搬运完数据, 产生 Complete Callback 的时候第二个 ADC 的数据还没有被搬运完成. 这样就会一个相电流是新数据一个相电流是旧数据, 不利于电流闭环控制.

进一步的, 我们发现 G431 的 ADC1 和 ADC2 可以同步工作, 然后公用一个 DMA, 这样就不会引起到底是哪个 DMA Complete Callback 对数据进行处理的混乱.
我们把 TIM1 的模式改为 **Dual regualr simultaneous mode only**, 然后使能 **DMA Access Mode**. 还要把 ADC1 的 DMA 改成 Peripheral 和 Memory 双 Word. 因为在 dual 模式下, ADC1 作为主 ADC, ADC2 的转换结果会存到 ADC1 高 16 位上. 这样就能只用 **一个 DMA** 就能同步搬运两个通道的数据了.

具体代码如下:
```c
HAL_ADC_Start(&hadc2);
HAL_ADCEx_MultiModeStart_DMA(&hadc1, adcBuffer, 2);
```

## 磁编码器 MA732 使用, 校准 与 滤波
**驱动**
工作在 **16 bit SPI** 模式下, 之前用 8 bit SPI 配合软件 CS 是错误的用法. 

MA732 内部有个很小的 FLASH, 能够掉电存储校准数据. 在调试中遇到了 16bit 高低位顺序等勾八问题, 在使用错误的配置与其通信的时候可能不小心把数据写入到校准区域, 导致后续读出来的数据错误, 可能是 0xFFFF 或者是 0x0000. 根据 datasheet 里的默认寄存器内容重置 MA732 后问题解决.

在使用 SPI 与其通信的时候, 读取不能使用 HAL_SPI_Receive, 因为单纯的 Receive 的时候 MOSI 可能会有脏数据, 导致意外的命令写入. 正确办法是开一个空 buffer, 然后使用 **HAL_SPI_TransmitReceive** 与其通信.

因为 ADC 的转换需要时间, 所以考虑用 Update Event 的同时, 用 Update Event 中断触发 **HAL_SPI_TransmitReceive_IT**, 然后在 SPI 的 **transmit Complete Callback** 里解码. 

**校准与归零**
使用磁编码器内部的 Flash 可以在任意的角度归零. 但是为了方便, 我们首先将机械角度(的极对数倍)对齐到电角度, 然后再将此编码器角度设为零, 以此实现磁编码器校准. 我们调用 calibrateEncoder() 之后就会自动进行校准, 校准结果写在 calibrationResult 里面, 需要在 ozone 里 watch 然后手动 hardcode 到 ENCODER_BIAS 里面, 注意需要补足一个 dummy byte ENCODER_BIAS[256] = ENCODER_BIAS[0], 方便运算.

实际上存到 ENCODER_BIAS 里的值是偏移值 / 2, 这样设计的目的是把偏移压缩进一个 byte, 一共 256 Byte. 其余的点通过**定点数运算**的**线性插值**快速得到.

**磁编码器自动校准**
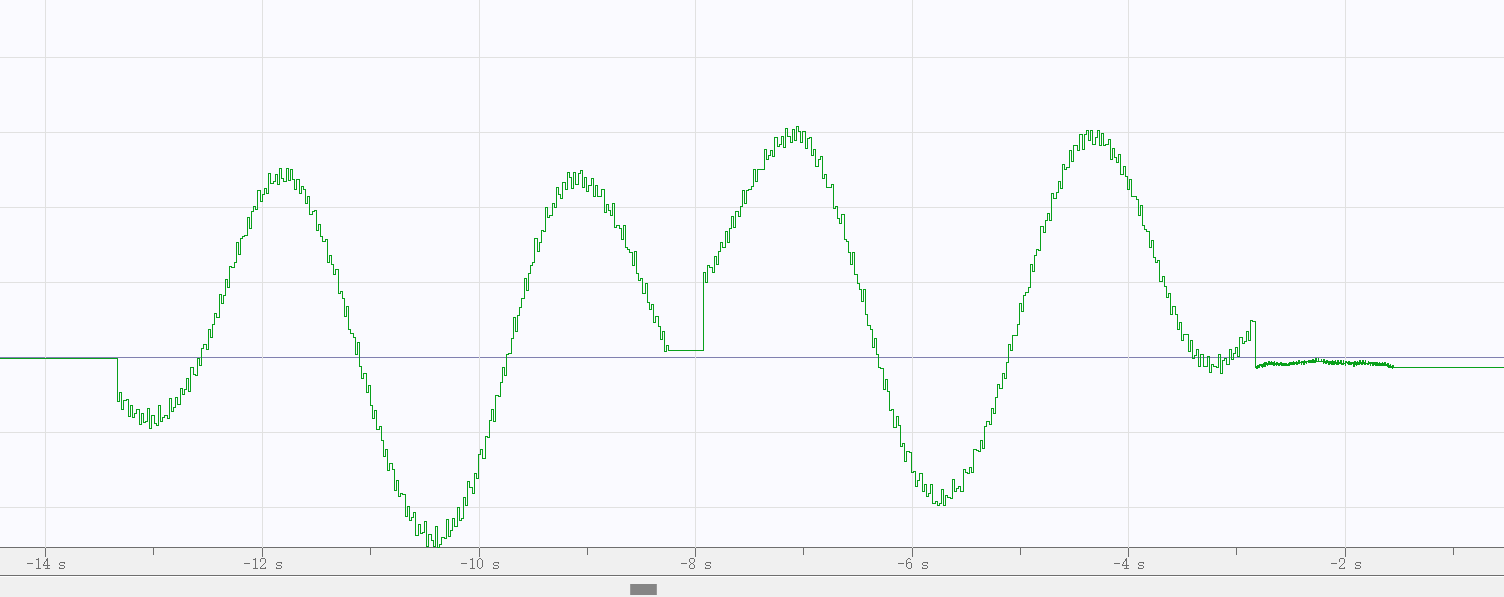
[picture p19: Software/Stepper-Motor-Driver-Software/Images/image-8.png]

上图的第一个周期是正转时, 开环电角度与读取到的角度的差值, 第二个周期是反转的, 第三个周期是正反转差值的差值.
我们想要验证的是, 正反转的时候, 开环磁场角度领先机械角度的角度是固定的, 因此我们可以通过正反转求平均消除这个影响.
校准完毕得到 calibrationResult 之后, 在 ozone 里 watch calibrationResult, 然后导出到 python_code 文件夹, python 脚本自动生成校准数据 ENCODER_BIAS.

!!! 似乎仍然有 bug. 校准得到的偏移数据起始约为 3, 但是终止约为 11, 看起来像是正转的时候转过头了或者转快了(起始位置比终止位置 encoderError 小不少). 很逆天的解决办法是, 正转 -> 反转 -> 反转 -> 正转 的顺序来四次取平均.

四次旋转校准之后, openloop 时的结果:
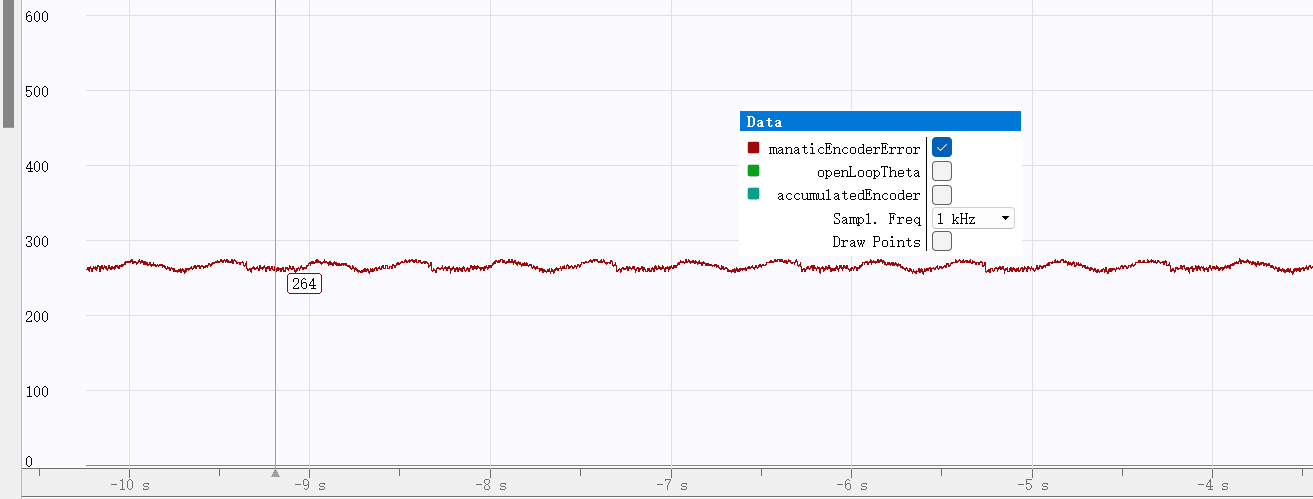
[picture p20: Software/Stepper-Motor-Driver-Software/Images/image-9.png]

可以看到, 在 openloop 情况下, 磁场角度稳定领先机械角度.
对比下图未校准情况, 有非常显著改进.
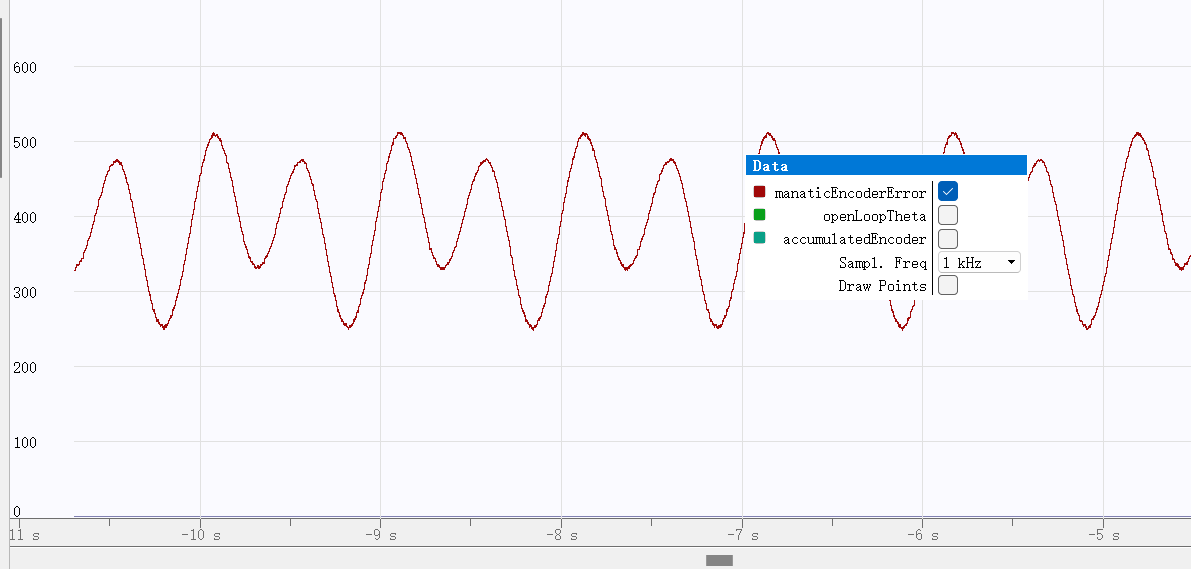
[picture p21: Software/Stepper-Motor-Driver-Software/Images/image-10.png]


**内部滤波**
内部有个带通滤波器, 延迟有点大, 我们将滤波器截止频率跳到 730 Hz, 降低其延迟. 这一点在多极对数的电机上很关键.
以下是不同内部滤波的统计数据:
|Cutoff Freq|标准差|
|:--|:--|
|3000Hz|7.4|
|1500Hz|6.5|
|730Hz|4.2|

**外部滤波**
因为磁编码器读取出来到参与电流环运算有时间间隔, 这里使用一个简单的 **卡尔曼滤波器** 对运算时刻的角度进行估计.
Update Event 以最高速度试图调用磁编码器, 在每次成功调用 HAL_SPI_TransmitReceive_IT 之后立即将时间戳清零(也可以为负数, 用于细微调节时间). 在之后的每一次失败调用里都将时间戳 += 1. 
同时, 我们要求 MA732 驱动维护一个近期瞬时速度(可用一阶低通滤波实现), 在电流环运算的时候, 通过 MA732 的时间戳与瞬时速度可以计算出运算瞬时的电角度.
可以同时建立无感观测器, 但是没有必要.

---

**卡尔曼滤波器**
我们需要观测电机的角位置和角速度, 我们能观测到的值是当前的角位置, 我们也从上一个 encoder 和当前 encoder 算出一个速度.
所以:

我们输入的矩阵是:
$
y_{k} = 
\begin{bmatrix}
\theta_{角度_k} \\
\omega_{角速度_k}
\end{bmatrix}
$

我们观测得出的矩阵是:
$
x_{k} = 
\begin{bmatrix}
\theta_{角度_k} \\
\omega_{角速度_k}
\end{bmatrix}
$

我们有已知的控制输入 $I_q$
可以算出扭矩
$\tau = I_q * K_q$
其中, $K_q$ 为扭矩常数.

进一步算出角加速度 $\alpha$
$\alpha = \frac{\tau}{J} = \frac{K_q}{J} * I_q$

---

我们假设运动的过程是匀加速运动, 我们写出运动学方程:
$\theta_{角度_k} = \theta_{角度_{k-1}} + \omega_{角速度_{k-1}} * dt + \frac{1}{2}\alpha_{角加速度_{k-1}}dt^2$
$\omega_{角速度_k} = \omega_{角速度_{k-1}} + \alpha_{角加速度_{k-1}}*dt$

写成卡尔曼状态转移矩阵就是:
$
\begin{bmatrix}
\theta_{角度_k} \\
\omega_{角速度_k}
\end{bmatrix} = 
\begin{bmatrix}
1 & dt\\
0 & 1
\end{bmatrix}
\begin{bmatrix}
\theta_{角度_{k-1}} \\
\omega_{角速度_{k-1}}
\end{bmatrix} +
\begin{bmatrix}
\frac{1}{2}dt^2 \\
dt
\end{bmatrix} * \alpha_{角加速度_{k-1}}
$
对应:
$\hat{x}_{k} = F \cdot x_{k-1} + B \cdot u_{k} + w_{k}$
所以
$F = 
\begin{bmatrix}
1 & dt\\
0 & 1
\end{bmatrix}$

$B = 
\begin{bmatrix}
\frac{1}{2}dt^2 \\
dt
\end{bmatrix}$

$u_{k} = \alpha_{角加速度_{k-1}}$

同时, 协方差的估计如下:
$P_{k} = F \cdot P_{k-1} \cdot F^T + Q$

$P_{k}$: 状态协方差矩阵的先验估计
$Q$: 过程噪声 $w_{k}$ 的协方差矩阵

**状态校正**
在这种特殊情况下, 我们的观测值能被传感器读取到, 所以 $H = I$.

$x_{k} = \hat{x}_{k} + K_{k} \cdot (y_{k} - H \cdot \hat{x}_{k})$
$P_{k} = (I - K_{k} \cdot H) \cdot P_{k}$

其中, 
${x}_{k}$: 当前时刻状态估计的后验值 (滤波器最终输出)
$\hat{x}_{k}$: 当前时刻状态估计的先验值 (从状态预测阶段获得)
$y_{k}$: 传感器观测出来的值
$H$: 观测矩阵 把真实状态空间映射成观测空间
$I$: 单位矩阵

**计算卡尔曼增益**
$K_{k} = P_{k} \cdot H^T \cdot (H \cdot P_{k} \cdot H^T + R)^{-1}$

可以看到, 对于角速度的预测, 卡尔曼滤波器的工作得非常好. 看不出任何延迟.
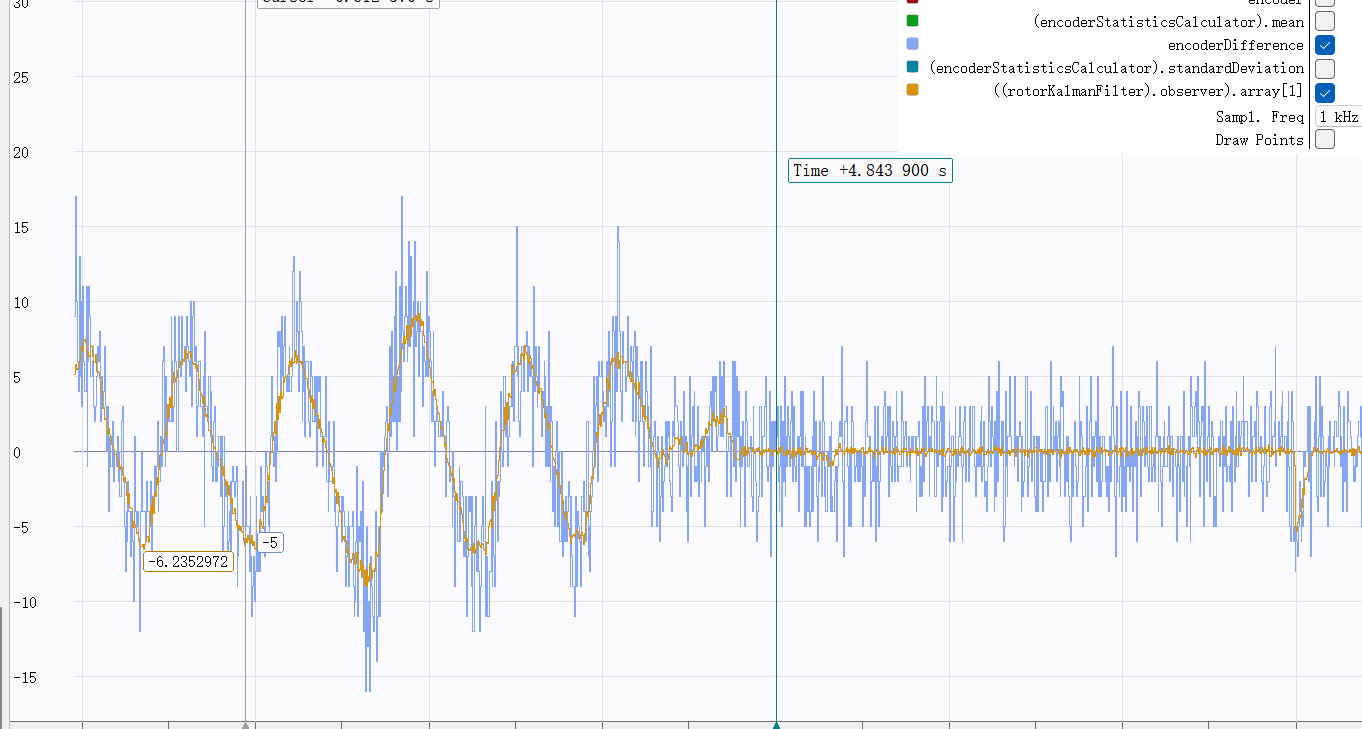
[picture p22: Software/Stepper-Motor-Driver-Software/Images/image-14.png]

去他妈的 操. 和一阶低通滤波器没有任何区别.  不玩了 一阶低通滤波牛逼.
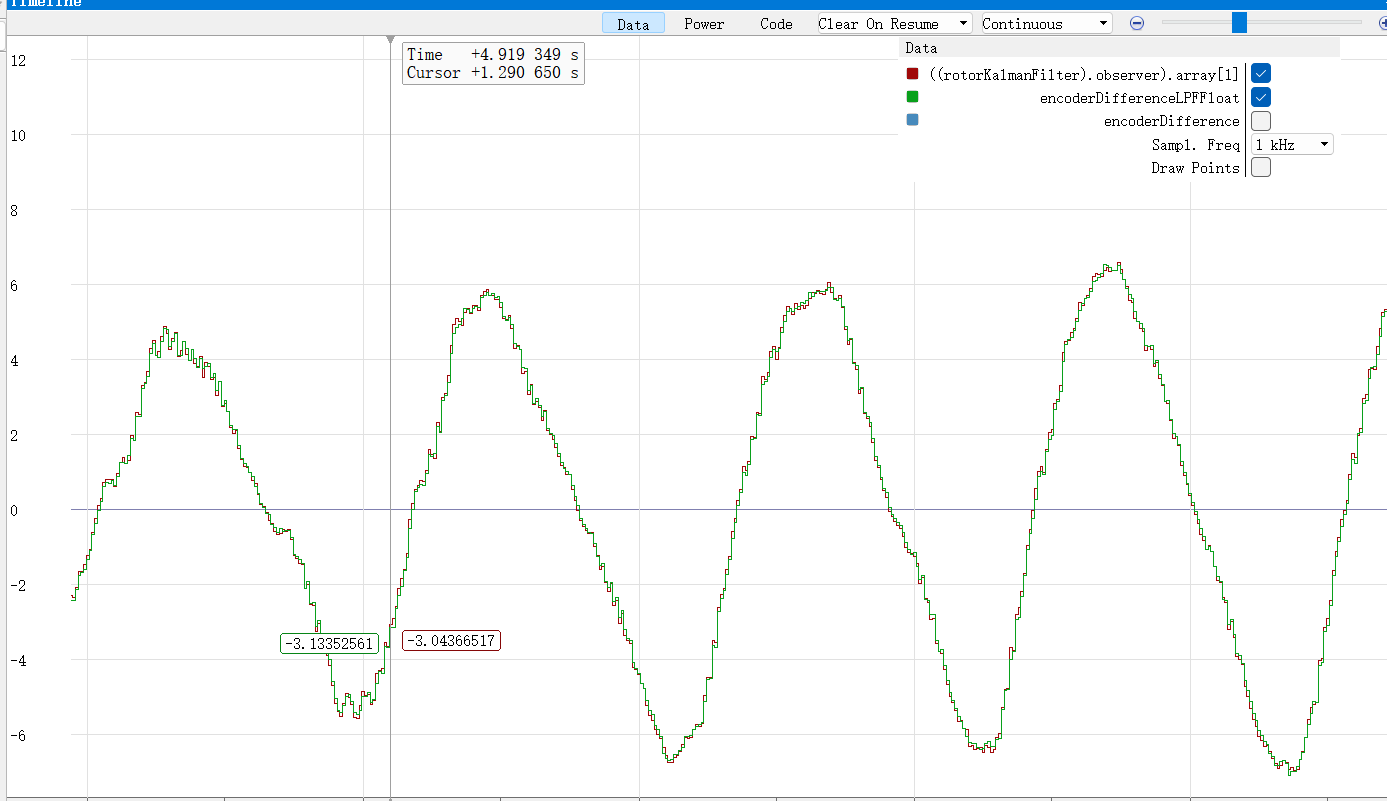
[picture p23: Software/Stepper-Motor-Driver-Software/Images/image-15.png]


## 磁编码器误差校准记录
对于缓慢的 SVPWM 固定速度开环强拖, 记录 SVPWM 输入角度与磁编码器读出角度的差值: 
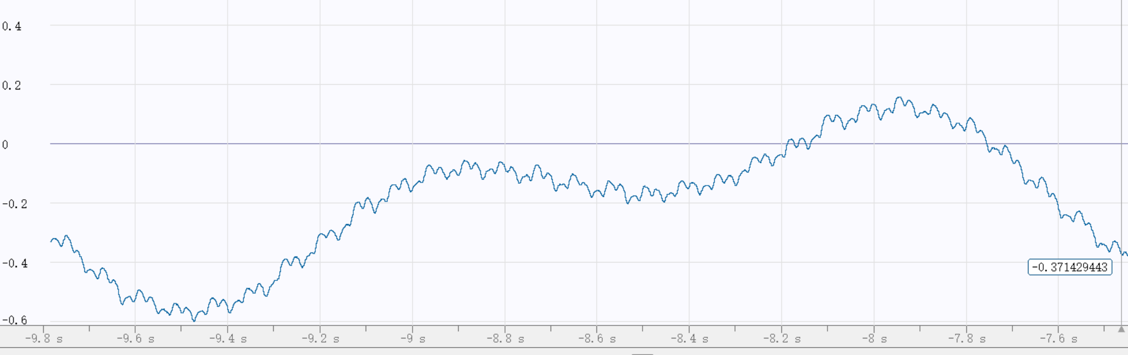
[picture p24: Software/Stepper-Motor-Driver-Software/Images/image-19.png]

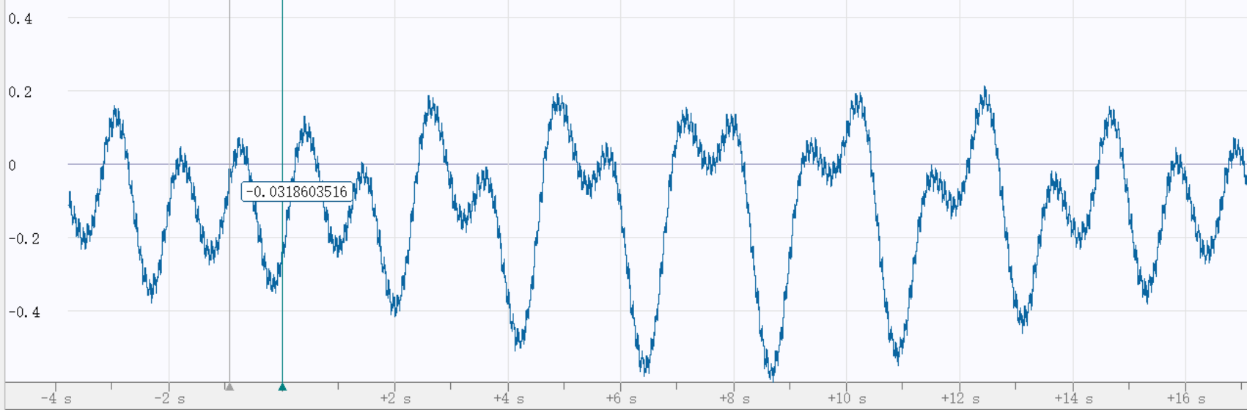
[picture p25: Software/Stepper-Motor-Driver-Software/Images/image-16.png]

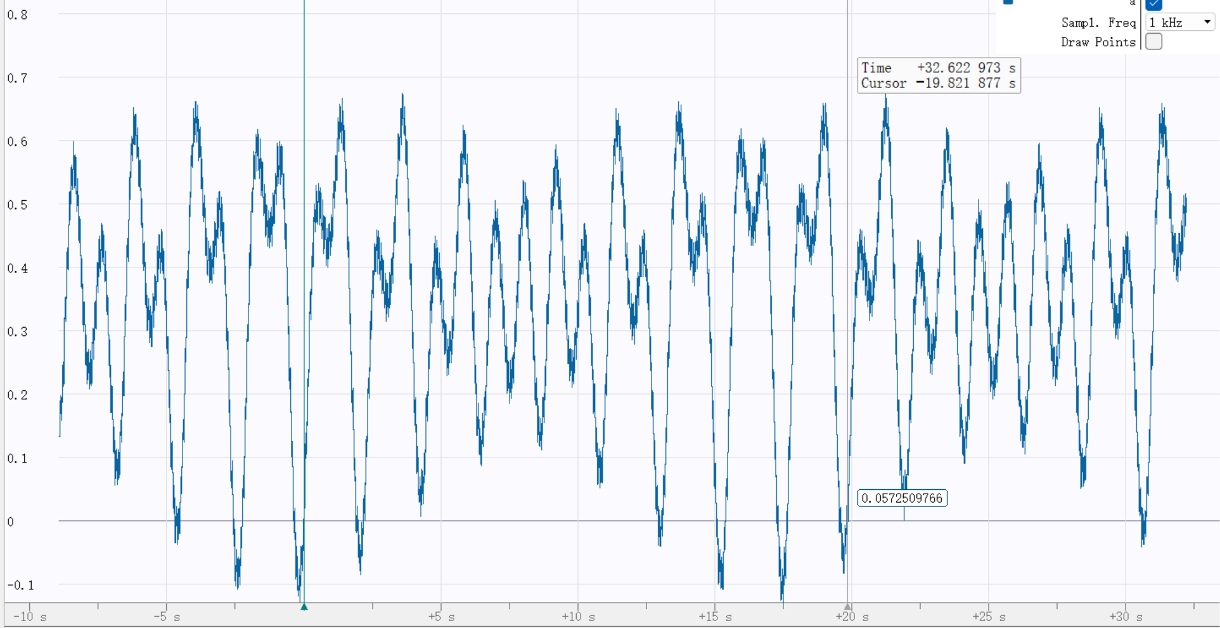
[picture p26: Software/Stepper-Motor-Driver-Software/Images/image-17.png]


进行单 electricAngle 采样并校正之后:
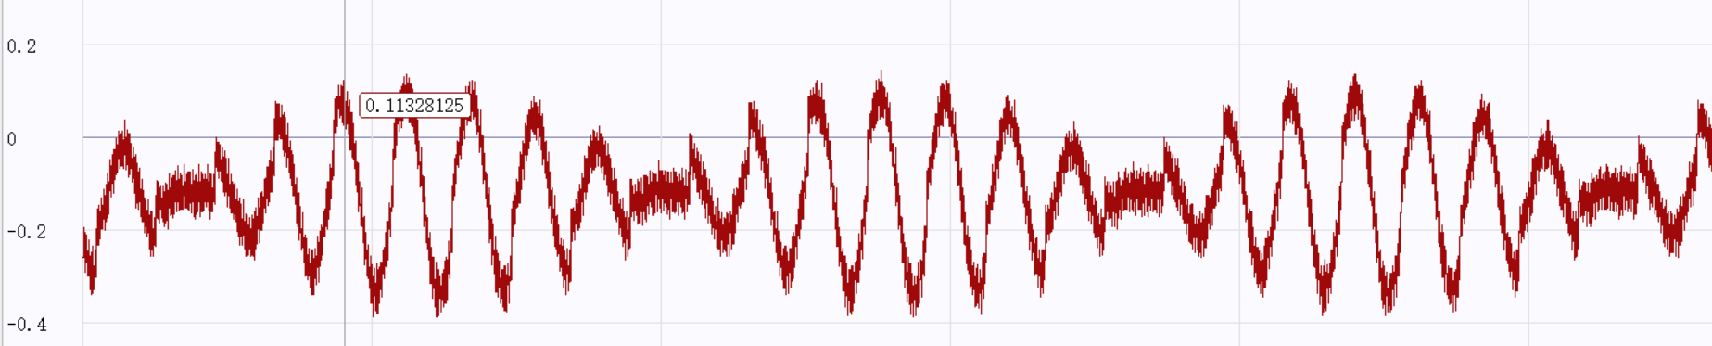
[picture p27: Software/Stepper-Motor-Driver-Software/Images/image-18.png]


这个波形一共由以下几个周期的波形组合而成:
1. (最高频) 周期等于 SVPWM 输入角度的周期, 即 electric angle 的周期. 在图上似乎是噪声, 但不是. 是由 **齿槽转矩 cogging torque** 产生的 称为 **齿槽效应 Cogging**. 齿槽转矩 是转子磁铁与定子线圈上的铁芯相互吸引导致的扭矩. 在没有电流的时候转转子的段落感的来源. 在转子旋转的时候会产生周期性的扭矩, 对抗驱动电流的扭矩. 相位与驱动角相位相同.
2. 一个猫猫波形: 周期等于电机转子转动周期. 由磁编码器与磁铁不同心安装, 不平行安装导致的. 相位提前或落后驱动角相位, 导致产生变形的正选波. 理论上来说每一周期的猫猫波形应该相似, 但是有其他原因导致问题.
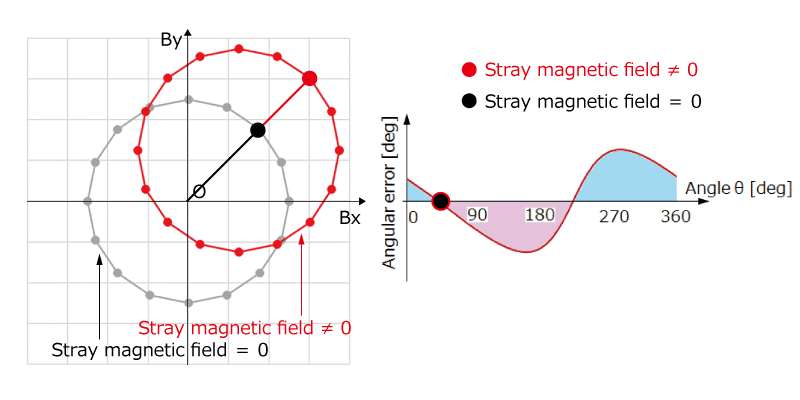
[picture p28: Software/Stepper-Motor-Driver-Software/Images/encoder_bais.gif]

3. 最大时间尺度的波形: 由减速箱导致的磁场. 周期是转子频率的 8 倍 (减速比)
在输出轴转动到同一位置的时候, 最大尺度的误差波形总是出现重复. 可以很肯定地说此误差与减速箱有关. 怀疑是减速箱磁化.
误差 peak-to-peak 值约为 300, 相当于 1.65° 轴角度和 23° 电角度. 此误差不可忽略.

> 波形分解解读参见:
> https://build-its-inprogress.blogspot.com/2017/03/encoder-autocalibration-for-brushless.html
> https://community.simplefoc.com/t/simplefoc-sensor-eccentricity-calibration/2212

拓展:
对于齿槽效应有以下几种改善方法: 
1. 线圈定子改为斜槽. 但是会降低效率.
2. 一片片磁铁改为磁环, 但是磁场强度小, 扭矩小.
3. 软件抗齿槽

使用 scipy.optimize.curve_fit, scipy.fft.fft 对误差波形进行拟合.
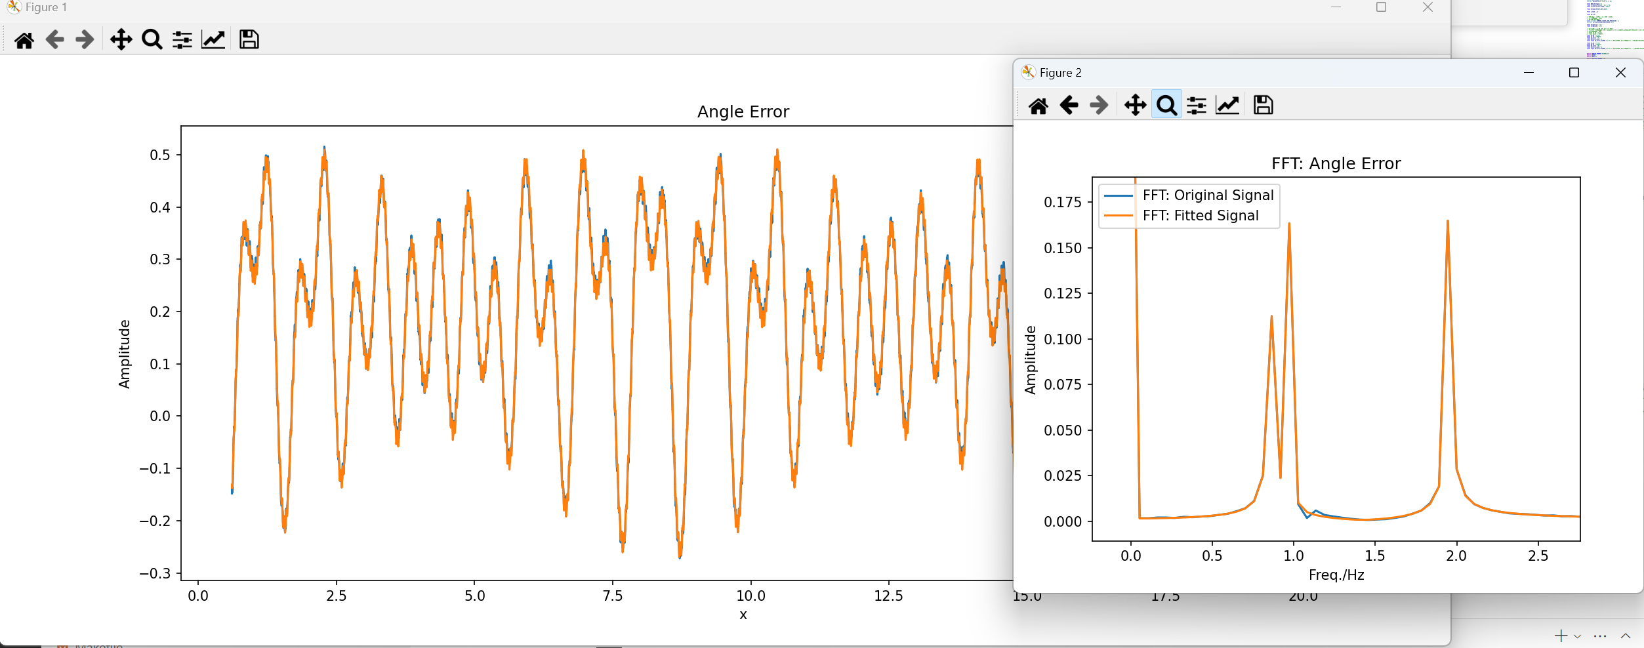
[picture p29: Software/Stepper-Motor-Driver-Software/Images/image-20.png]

在三个正弦叠加下可以拟合低频波, 六个正弦可以抵消齿槽效应.

## Park 变换与 FOC 闭环控制思路

我们使用 G4 的 Cordic 外设来计算三角函数, 同时乘上系数. 我们发现, 磁编码器的最高精度是 16 bit, 输出 PWM 精度约为 10 bit, 因此采用 15 bit 的 cordic 已经足够.
16 bit 模式的 cordic 可以在一个 32 bit 输入里面同时把两个输入参数打包进来.
具体使用方法参见:
> https://www.st.com/resource/en/reference_manual/rm0440-stm32g4-series-advanced-armbased-32bit-mcus-stmicroelectronics.pdf
> https://shequ.stmicroelectronics.cn/thread-635016-1-1.html

以下是 15bit 精度的示例代码:
```c
int32_t dualFloatToCordic15(float valueA, float valueB)
{
    int32_t CORDIC15;
    CORDIC15 = (int32_t)(valueB * 0x8000) << 16;
    CORDIC15 = CORDIC15 | (int32_t)(valueA * 0x8000);
    return CORDIC15;
}

void cordic15ToDualFloat(int32_t CORDIC15, float *valueA, float *valueB)
{
    // 处理高16位
    if (CORDIC15 & 0x80000000) // 为负数
    {
        *valueB = ((float)((CORDIC15 >> 16) & 0x7FFF) - 0x8000) / 0x8000;
    }
    else // 为正数
    {
        *valueB = (float)((CORDIC15 >> 16) & 0xFFFF) / 0x8000;
    }
    
    // 处理低16位
    if (CORDIC15&0x8000) // 为负数
    {
        *valueA = ((float)(CORDIC15 & 0x7FFF) - 0x8000) / 0x8000;
    }
    else // 为正数
    {
        *valueA = (float)(CORDIC15 & 0xFFFF) / 0x8000;
    }
}

static float cordicOutputSin1;
static float cordicOutputCos1;
static float cordicOutputSin2;
static float cordicOutputCos2;
hcordic.Instance->WDATA = dualFloatToCordic15(0.6667, 0.99999);
cordic15ToDualFloat((int32_t)(hcordic.Instance->RDATA), &cordicOutputSin1, &cordicOutputCos1);
hcordic.Instance->WDATA = dualFloatToCordic15(0.6667, 0.99999);
cordic15ToDualFloat((int32_t)(hcordic.Instance->RDATA), &cordicOutputSin2, &cordicOutputCos2);
```

> 可能可行的控制点: 在目标移动到距离目标位置小于一个 electricAngle 周期的之后, 增加给定固定位置的磁场.
> 目前输出的 Id Iq 在输出之前都会进行 Park 变换, 都会用到当前磁编码器的角度, 这可能会带来一些控制上的滞后性.
> 如果引入绝对位置的磁场, 可能可以增强响应.

---

targetIq 是内部的扭矩电流, 由速度位置 PID 算出来.
motorControlStatus.targetTourque 是最大扭矩. 在速度位置 PID 不工作的时候才用这个 motorControlStatus.targetTourque

### 坐标系变换的幅值转换
到底是选择等幅值变换还是等功率变换? 等幅值用的比较多. 这样采样得到的电流, 即相电流的幅值等于 Iq Id 的幅值. 然后在生成电压的时候直接生成相电压.
所以在传入 setPhaseVoltage 之前我们的限幅就不是 24 V 了, 而是根据上文限制到 $12\sqrt{3} V$

## 电流环 PI 控制器设计, 前馈与抗饱和

**前馈**
根据 https://blog.csdn.net/qq_39360369/article/details/121693910 的推导可知, dq 轴的状态方程中存在耦合项, 即 dq 电流会互相影响. 前馈的作用是是将 dq 轴解耦, 一方面是交叉解耦, 另一方面是抵消反电动势.
通过下面这个图设计前馈, 需要获取相电阻, 相电感, KV 值.
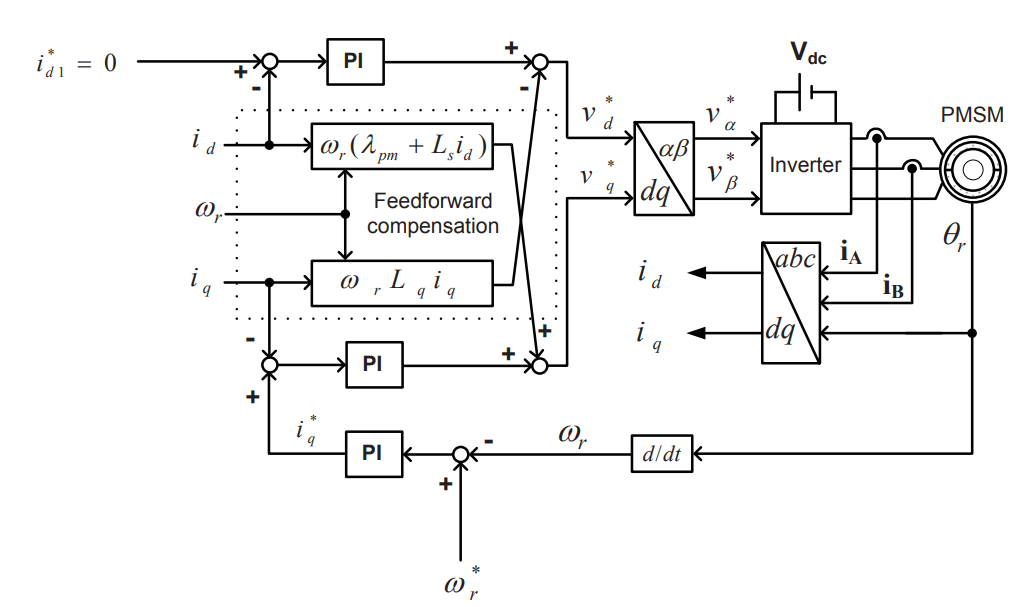
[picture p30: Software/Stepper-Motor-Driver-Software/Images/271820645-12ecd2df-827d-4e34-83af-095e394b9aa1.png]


可以看到, 前馈直接加到 PI 控制器的输出结果上, 数学表达是:
```
//   Resistance  Inductance   Cross terms   Back-EMF   (see www.mathworks.com/help/physmod/sps/ref/pmsm.html)
vd = Rs*id   +   Ld*did/dt −  ωe*iq*Lq
vq = Rs*iq   +   Lq*diq/dt +  ωe*id*Ld     + ωe*ψm
```

我们转换变量名称, 也就是:
```c
backwardEMF = SPEED / KV;
Vq += Rs * Iq + SPEED * Ld * Id + backwardEMF;
Vd += Rs * Iq - SPEED * Lq * Iq;
```
> https://github.com/simplefoc/Arduino-FOC/issues/317

**弱磁控制**
取磁通量 $\lambda$. 我们知道, 线圈里的电流需要在每个周期内反向, 因此磁通量也反向. 当线圈里的最大磁通量越大, 在同等速度下, $\frac{d\lambda}{dt}$ 越大, 因此反电动势 bEMF 越大. 所以, 降低线圈里的磁通能够提高电流变化所需时间, 从而提高转速.
弱磁控制 weakened field control 的目的就是降低磁通, 以达到超过最大速度的速度.

弱磁控制的核心在于 \[TODO\]

## 速度环/位置环竞争 PID
速度环刷新频率为 4000Hz, 位置环刷新速率为 1000Hz.
不采用竞争方式. 竞争 PID 可以防止过冲位置. 
但是我们采用串级 PID. 这样在控制移动到目标位置的时候可以同时控制速度.

## 保护
**错误类型**
1. 三相电流和不为 0
2. 磁编码器断联
3. 相断联
4. 驱动器 FAULT
5. 驱动器 过温 Warning
6. 驱动器 过温 FAULT
7. 电机线圈过温
8. 过流
9. 欠压过压
10. 控制包非法

## 错误处理与状态机
用 ErrorHandler.c 实现的错误处理与自动恢复. 
motorErrorStatus.driverFault 和 FAULT 全局变量同步.
当 FAULT 被电机驱动触发, 而且电机是 enable 状态, 立即 disable 电机.
出现欠压, 过压, 过流, 过温会通过对应 Counter 延迟触发.

在非 FAULT 错误不在发生的时候, 会通过 Counter 自动恢复.

Optional: 当检测到电机被 disable, 而且所有错误都不再发生的时候, 可以自动 enable 电机.

## 通信
通信协议如下

所有数据都是 int16_t 类型.

主控板发送控制包:
CAN ID: 0x100 + ID = 0x101~0x108
```
        | 7 | 6 | 5 | 4 | 3 | 2 | 1 | 0 |
Byte 0: | 0 |      Control MASK         |
Byte 1: |          Control Data         |
Byte 2: |             Data              |
Byte 3: |             Data              |
Byte 4: |             Data              |
Byte 5: |             Data              |
Byte 6: |             Data              |
Byte 7: |             Data              |
```

1. 当 Byte 0 的 Bit 7 == 0
    * Byte 0:   Control MASK
        * Bit 7: 0
        * Bit 6: 位置设置 MASK                          0: 不修改, 1: 修改
        * Bit 5: 速度设置 MASK                          0: 不修改, 1: 修改
        * Bit 4: 扭矩设置 MASK                          0: 不修改, 1: 修改
        * Bit 3: 忽略错误 MASK                          0: 不修改, 1: 修改
        * Bit 2: 自动复位 MASK                          0: 不修改, 1: 修改
        * Bit 1: RGB 控制 MASK                          0: 不修改, 1: 修改
        * Bit 0: 使能输出 MASK                          0: 不修改, 1: 修改

    * Byte 1:   Control Data
        * Bit 7: 手动触发复位?                          0: 无效, 1: 复位    推荐: 0
        * Bit 6: 位置 Byte 是否有效(是否闭环位置)?      0: 无效, 1: 有效    推荐: 1
        * Bit 5: 速度 Byte 是否有效(是否闭环速度)?      0: 无效, 1: 有效    推荐: 1
        * Bit 4: 扭矩 Byte 使用电流闭环还是电压控制?    0: 电压, 1: 电流    推荐: 1
        * Bit 3: 强制忽略所有错误?                      0: 否,   1: 是      推荐: 0
        * Bit 2: 自动复位?                              0: 否,   1: 自动复位推荐: 0
        * Bit 1: 谁控制管理 RGB?                        0: 电机, 1: 主控板  推荐: 0
        * Bit 0: 是否使能输出?                          0: 禁用, 1: 启用    推荐: 1

    * Byte 2: 最大扭矩电流(加速度) 高 8 位
    * Byte 3: 最大扭矩电流(加速度) 低 8 位
    * Byte 4: 目标速度 高 8 位
    * Byte 5: 目标速度 低 8 位
    * Byte 6: 目标位置(增量) 高 8 位
    * Byte 7: 目标位置(增量) 低 8 位

2. 当 Byte 0 的 Bit 7 == 1
    * Byte 0:
        * Bit 7: 1
        * 其他位: 保留
    * 其他 Byte: 保留

    * Byte 5: LED 颜色 R
    * Byte 6: LED 颜色 G
    * Byte 7: LED 颜色 B

电机返回状态包:
CAN ID: 0x200 + ID = 0x201~0x208

Byte 0: 电机运行状态
    * Bit 7: 0
    * Bit 6: 位置闭环?                              0: 电压, 1: 电流
    * Bit 5: 速度闭环?                              0: 否,   1: 是
    * Bit 4: 电压/电流控制?                         0: 电压, 1: 电流
    * Bit 3: 强制忽略所有错误?                      0: 否,   1: 是
    * Bit 2: 是否会自动复位?                        0: 否,   1: 自动复位
    * Bit 1: RGB 谁控制?                            0: 电机, 1: 主控板
    * Bit 0: 电机是否使能                           0: Dis   1: Enable

Byte 1: 错误状态
    * Bit 7: 控制包解码错误?                        0: 无,   1: 有
    * Bit 6: 过温 Warning?                          0: 无,   1: 有
    * Bit 5: 过温错误?                              0: 无,   1: 过温
    * Bit 4: 过流错误?                              0: 无,   1: 过流
    * Bit 3: 欠压 过压错误 ?                        0: 正常, 1: 欠压或过压
    * Bit 2: 是否堵转?                              0: 无,   1: 有
    * Bit 1: 驱动器 FAULT?                          0: 无,   1: 有
    * Bit 0: 电机是否有 Error?                      0: 无,   1: 有

Byte 2: 实际转矩电流 高 8 位
Byte 3: 实际转矩电流 低 8 位
Byte 4: 编码器(输出轴单圈位置) 高 8 位
Byte 5: 编码器(输出轴单圈位置) 低 8 位
Byte 6: 到目标位置的执行进度(0~100%)

## BUG Record
测试发现, 给定固定 Ud!=0, Uq = 0 都能使其微弱转动, 且给定初始速度时, 仿佛有较大转动惯量, 很难启转停转. 可能是 timing 的问题(磁编码器采样时机/延迟)的问题.
示波器测量后发现, 在 enableFOCUpdate = 1 的时候, timer update event 的时机都发生变化, 具体是在正好最低点和最低点往右 1/4 个周期内浮动. 且变化速率很高. 在 enableFOCUpdate = 0 的时候,  timer update event 触发符合预期. 继续测量, 发现在 enableFOCOutput = 0, enableFOCUpdate = 1 的时候也正常. 推测是电流环里某些代码执行过慢导致的.
最终二分法定位到是如下代码段执行之后, update event, 电流环触发时机开始变得不稳定:
```
if(forceUd != -12345.0)
{
    outputUd = forceUd;
}
if(forceUq != -12345.0)
{
    outputUq = forceUq;
}

if(outputUq > 0.4)
{
    outputUq = 0.4;
}
else if(outputUq < -0.4)
{
    outputUq = -0.4;
}

if(outputUd > 0.4)
{
    outputUd = 0.4;
}
else if(outputUd < -0.4)
{
    outputUd = -0.4;
}
```

用 gpio 配合示波器进行分析, 发现是 MA732 与 SPI 读写过慢. 时序如下:
```
以下为实际时间:
0    us     Update Event
0.2  us     进入 MA732_Read()
1.5  us     离开 MA732_Read()
4.2  us     MA732 CS 下拉
5    us     MA732 CS 上拉
5.52 us     HAL_ADC_ConvCpltCallback 被调用, 正式进入电流环
16.9 us     HAL_SPI_TxRxCpltCallback 被调用, MA732 被读到.
```

可以看到 HAL_SPI_TxRxCpltCallback 非常晚才被调用, 甚至晚于电流环. 所以 HAL 库 SPI 纯勾八, 死慢.
我们换成 LL 库, 直接操作寄存器, 进行阻塞的 SPI 读写. 需要考虑在 timer update event callback 里阻塞是否有问题, 因为有可能是在 timer update event callback 执行完之后才触发 ADC 转换的.
我们懒得读实际代码, 我们直接做个实验:
在 TIM1_UP_TIM16_IRQHandler 里什么都不做, 和进行一大堆翻转 GPIO 的操作, 用来延时, 然后看进 adc Complete callback 的时间会不会变
进行垃圾操作之后, 5.7us 进 ADC Complete Callback
不进行垃圾操作, 3.36us 进 ADC Complete Callback
说明, ADC 是在 timer update event callback 之后触发的. 

---

但是, 我们注意到, 在 timer update event callback 里面有个 HAL_TIM_IRQHandler(&htim1); 我们刚刚是在它前面做垃圾操作的, 有没有可能 HAL_TIM_IRQHandler 就是用来触发 ADC 的?
我们尝试在 HAL_TIM_IRQHandler 之后做垃圾操作, 如果 adc 没有被延迟触发, 则我们的猜想正确.
在进入 TIM1_UP_TIM16_IRQHandler 之后的 1.7 us, 垃圾操作开始. 
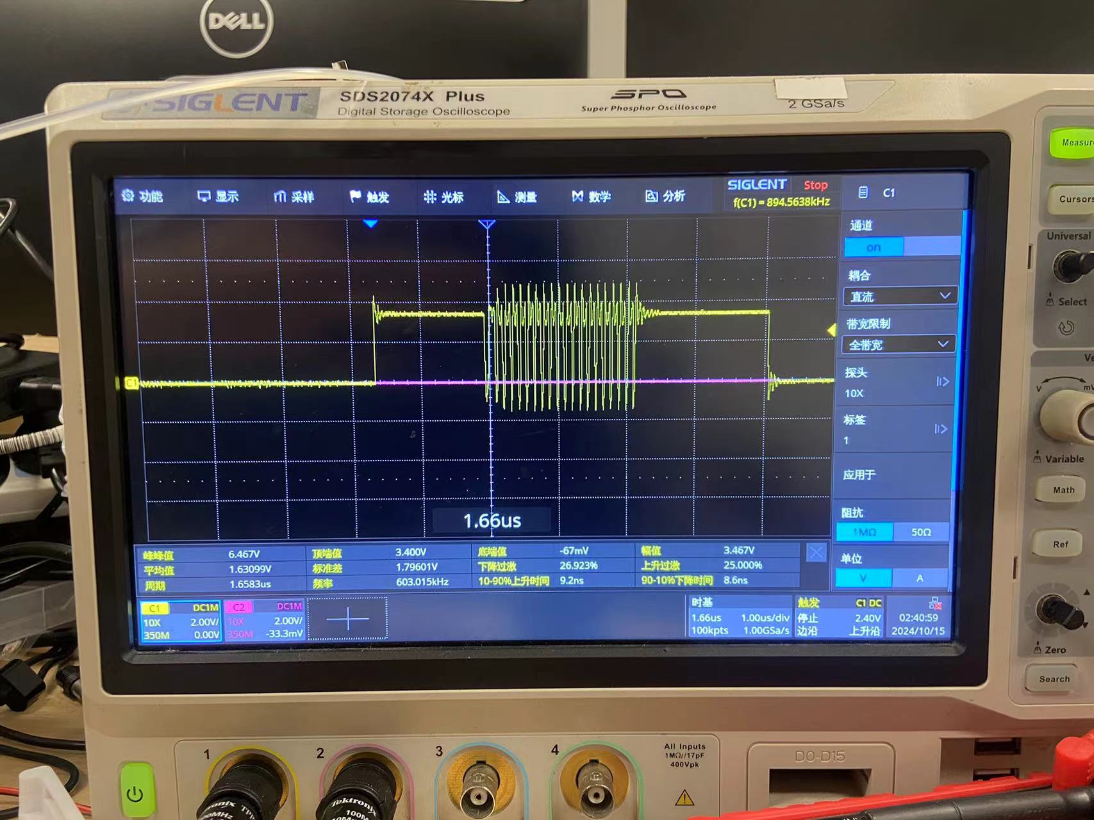
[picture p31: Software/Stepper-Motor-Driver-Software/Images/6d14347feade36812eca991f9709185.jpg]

而在 5.7us 之后, adc Complete callback 被成功触发! 和原来的时间完全一样! 我们的猜想正确!
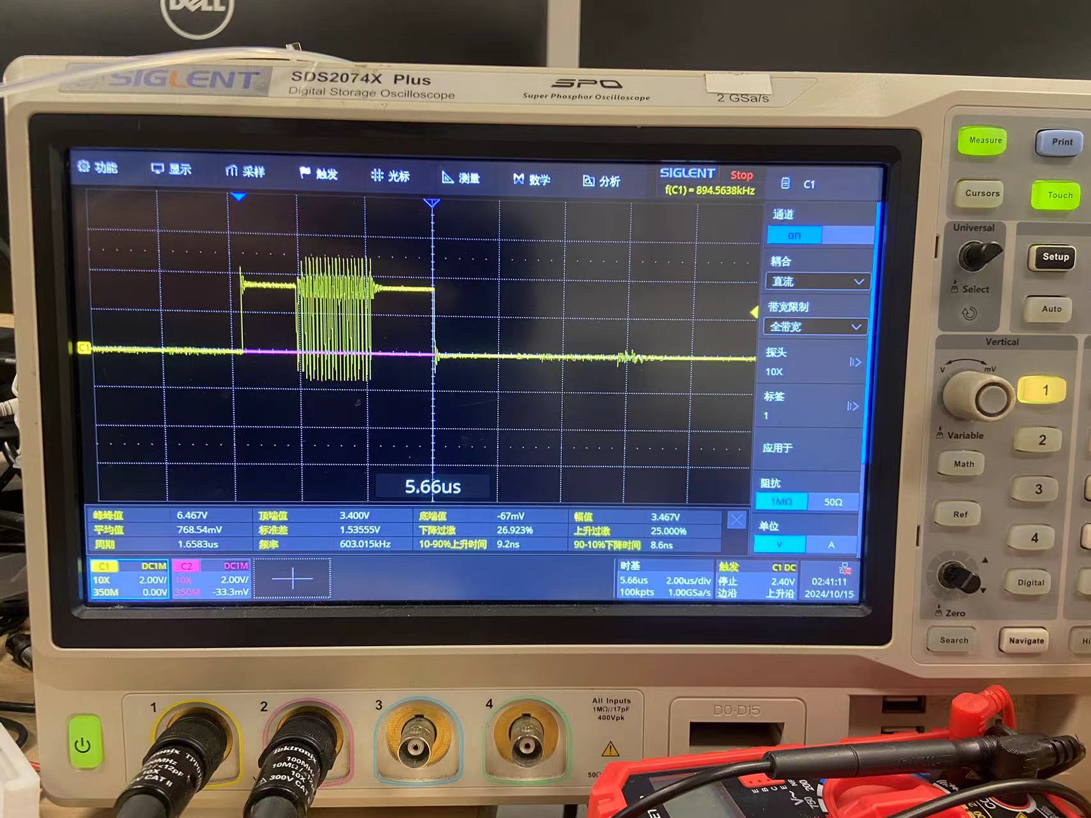
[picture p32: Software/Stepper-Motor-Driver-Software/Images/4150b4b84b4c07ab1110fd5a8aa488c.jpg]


以上结果说明, 在 STM32CubeMX 里配置的用 TIM1 Update Event 对 ADC 进行触发, 实际上不是硬件连接, 而是通过中断完成的. TIM1 Update Event 会调用  timer update event callback, 而在 callback 里的 HAL_TIM_IRQHandler 里面对 adc 完成了触发. 可惜的是, 我没能在 HAL_TIM_IRQHandler 代码里找到与触发 adc 相关的具体代码. 算了.

---

观察到, 在电机运动时, 给定一个反方向的瞬时力, 会导致电机反方向运动抖动. 在给定较大 Iq 时, 用手摁住电机能造成周期性的抖动.
尝试排除 Id 的影响, 将 Ud 强制设为 0. 观察波形得到, 抖动的过程分为两部分:]

在抖动第一个瞬间Uq 没有剧烈变化但是 Id 和 Iq 迅速改变极性.
观察 electricAngle 发现, 电机运动的方向瞬时改变



, Uq 没有剧烈变化但是 measueredId 和 measueredIq 发生了明显抖动:


这个现象似乎只在反方向突然加速的时候出现.
经过测试, 认为是丢步导致. 但是按理来说磁场方向应该时刻与磁铁垂直, 不应该出现丢步的情况, 除非刷新率不够.

上述现象在加入 EMF 的前馈以及 dq 解耦前馈之后得到了部分解决.
现在的现象变为, 在突然收到外部扭矩的时候会出现类似丢步的现象. 经过调整, 现象变为, 给定 Iq, 用刚体卡死电机, 此时稳态正常.
但是轻微地手动反向旋转, 电机输出扭矩会突然减小, 然后开始反向运转. 

**解决方案**
将磁编码器换为 MA732, 同时调高内部滤波器截止频率. 电流一下就闭了. 位置也一下闭了.

---

在开环转动的时候, 发现磁编码器位置有恒定变化的偏差. 在持续运行的时候偏差越来越大.
怀疑是浮点数误差导致的 浮点数的 significant 只有 20 bit, encoder 有 16 bit, 在转动 8 圈的时候就超过浮点数精度了. 所以改为 uint32_t.
全系列修改为定点数之后, 浮点数误差消除, 误差不再随着时间累加. 而是周期性变化.


---

在高速运转下, 会很偶尔出现卡顿, 观察发现是 electricAngluarVelocity 突然计算错误. 但是其他数据一切正常. 原因不知.


---

在 Uq=0.1, Ud=0 的情况下, 进行高速运动会疯掉. 具体表现见视频 1.mp4, 2.mp4
同时, 在 Uq = 0.

设为 Uq=0.0, Ud=0.2 有和上述一样的效果. **可能关键** 经过观察, 发现力突然减小的时刻发生在 measuredId 从 >0 变为 <0 的瞬间发生:

> 第一个峰谷 Id > 0, 此时没有失控, 第二个 Id < 0, 转矩突然减小, 电机失控.

同时观察到, 在失控起飞的过程中, measuredIq 和 measuredId 波形出现高频噪声. 且方向不断反向.

怀疑是磁编码器角度落后导致的 Iq Id 反 park 错误. 也有可能是测量到了电机反电动势造成的反向电流

将磁编码器换为 MA732, 同时调高内部滤波器截止频率之后, 丢步问题解决.

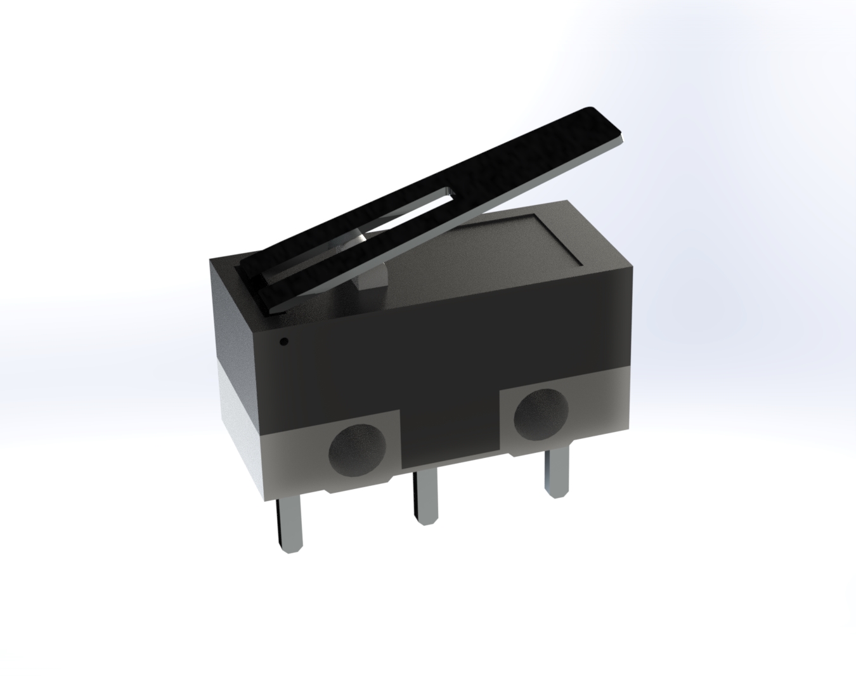
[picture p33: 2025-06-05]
Mechanical/short-lever-micro-switch/Short Lever MicroSwitch.jpg

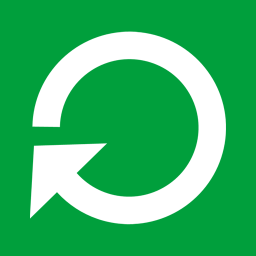
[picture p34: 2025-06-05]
Software/ClosePnP/Image/reRun.png

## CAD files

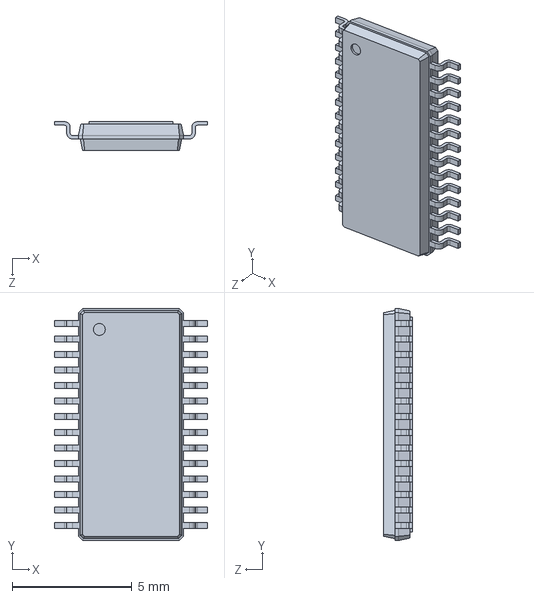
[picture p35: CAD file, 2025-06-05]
Mechanical/板支架/HTSSOP-28-1EP_4.4x9.7mm_P0.65mm_EP3.4x9.5mm.SLDASM
6.40 x 9.70 x 1.20 mm

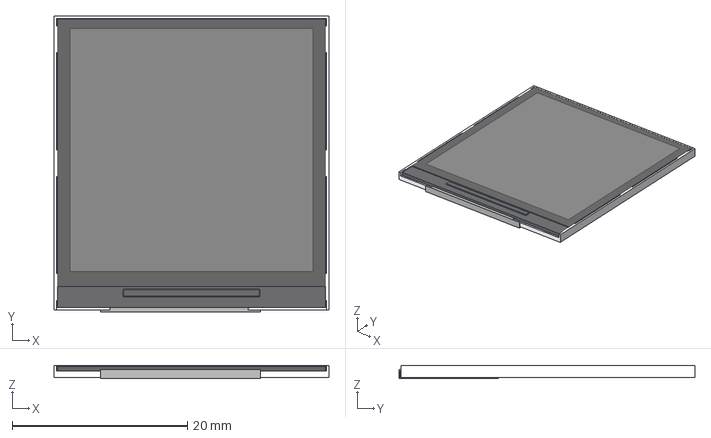
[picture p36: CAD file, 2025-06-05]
Hardware/1-KicadLibrary/1.54 TFT IPS - 12P - Flat Flush Mount.stp
31.4 x 33.8 x 1.54 mm

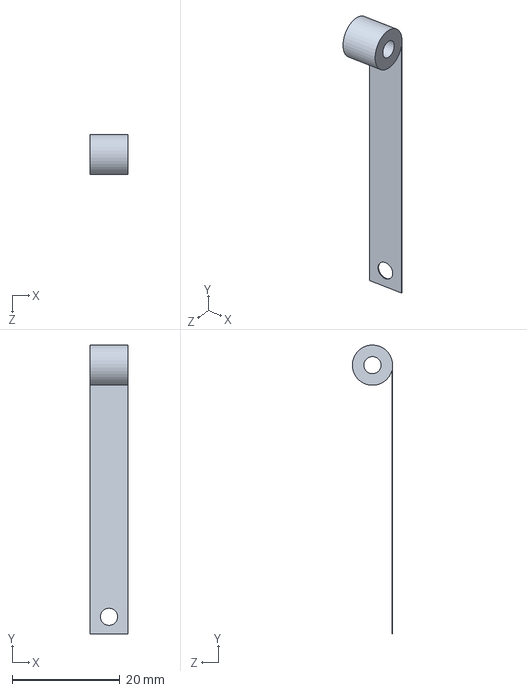
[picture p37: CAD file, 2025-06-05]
Mechanical/0.15_7_7拉簧.SLDPRT
7.00 x 53.7 x 7.49 mm

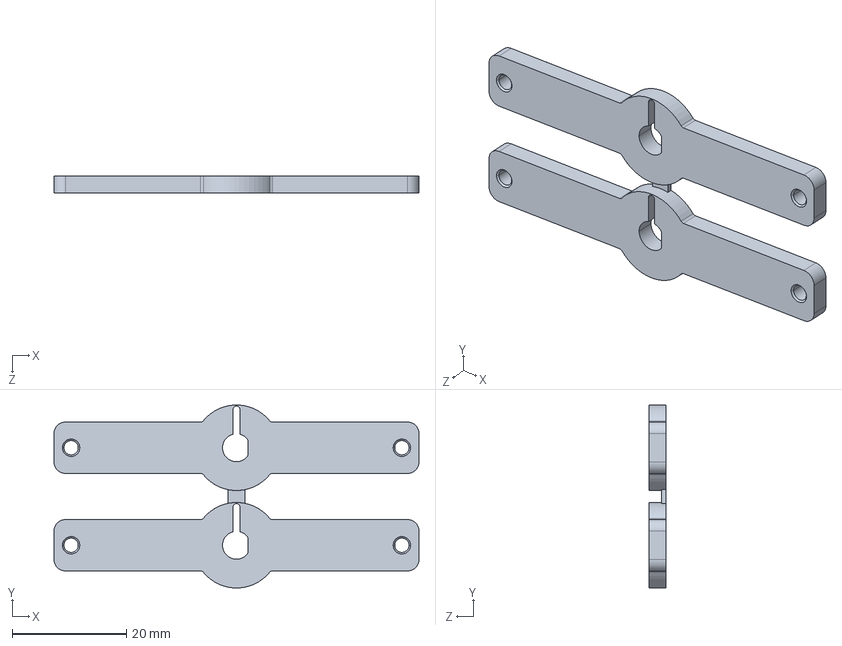
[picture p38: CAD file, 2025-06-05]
Mechanical/Production/3DP/Dual Head/摇臂.STEP
64.0 x 32.1 x 3.00 mm

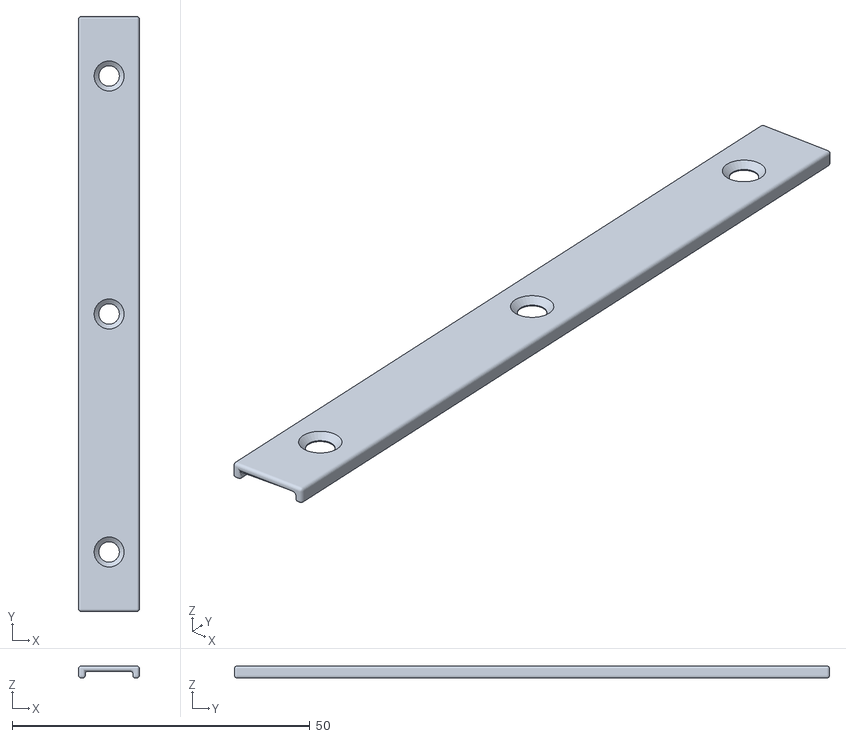
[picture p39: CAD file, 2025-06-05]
Mechanical/Production/3DP/SMT-Machine/feeder_cap.stl
10.2 x 100.0 x 2.02

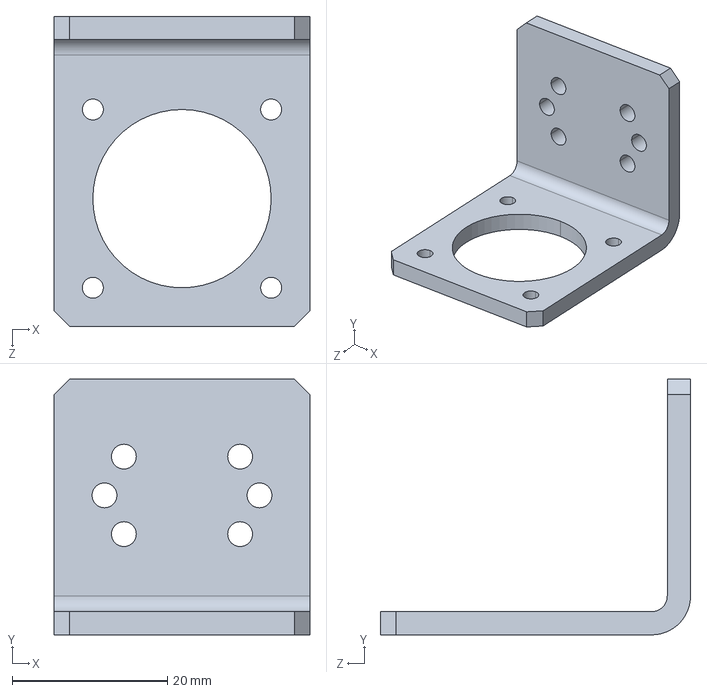
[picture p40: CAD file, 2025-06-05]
Mechanical/Production/钣金/RotateMotorL.STEP
33.0 x 33.0 x 40.0 mm

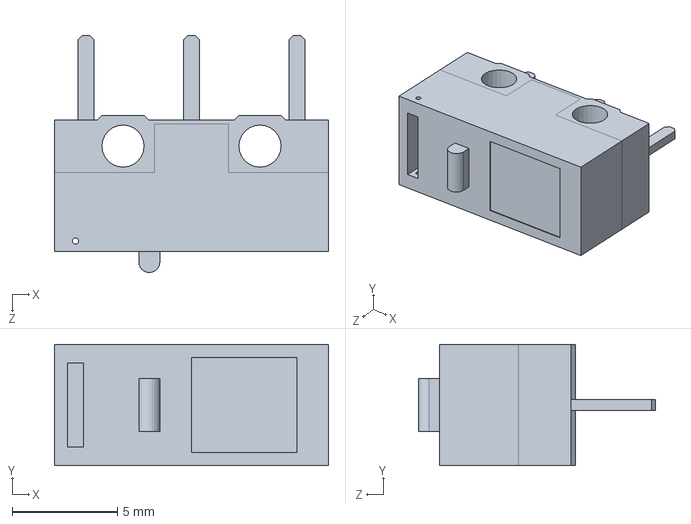
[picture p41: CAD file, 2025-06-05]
Mechanical/short-lever-micro-switch/Micro Switch.SLDPRT
13.0 x 5.75 x 11.2 mm

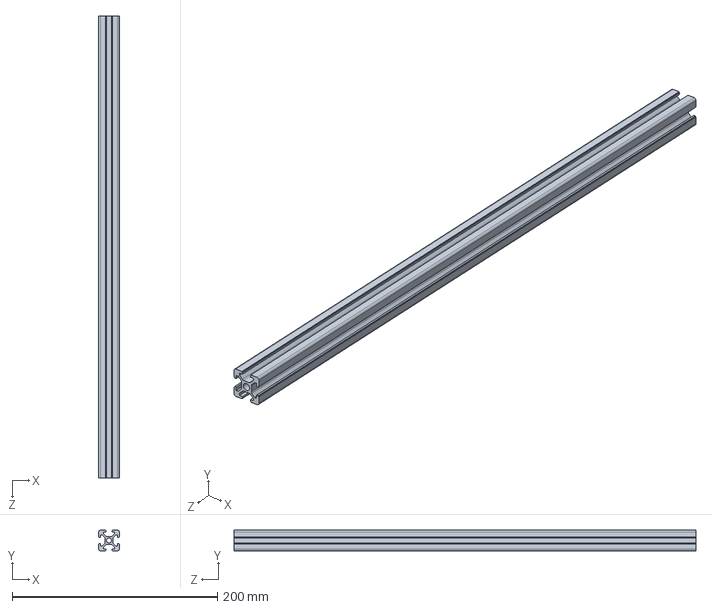
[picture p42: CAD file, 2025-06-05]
Mechanical/StandardPart/2020_AlTube_Front_Down.SLDPRT
20.0 x 20.0 x 450.0 mm

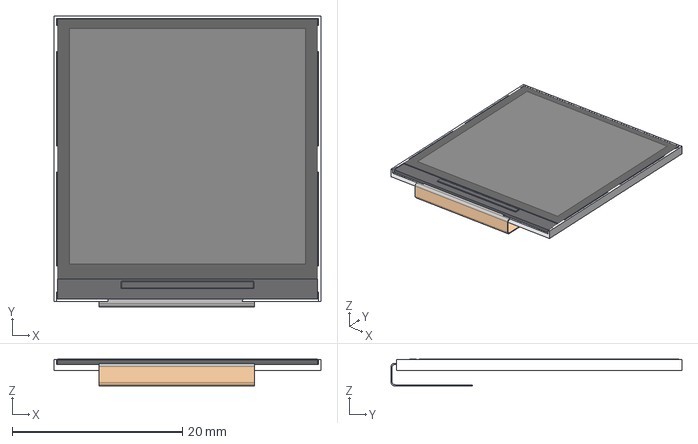
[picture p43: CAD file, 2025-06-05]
Hardware/1-KicadLibrary/1.54 TFT IPS - Reverse Mount.stp
31.4 x 34.2 x 3.16 mm

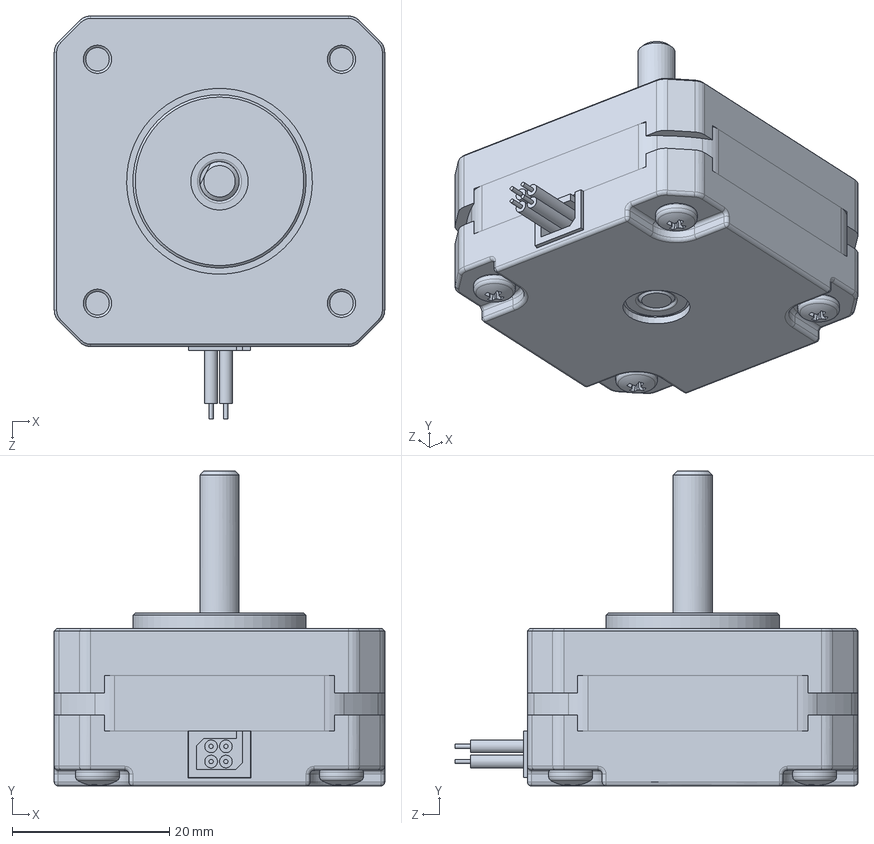
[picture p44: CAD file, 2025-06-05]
Mechanical/17HS08-1004S.SLDPRT
42.0 x 40.0 x 51.2 mm

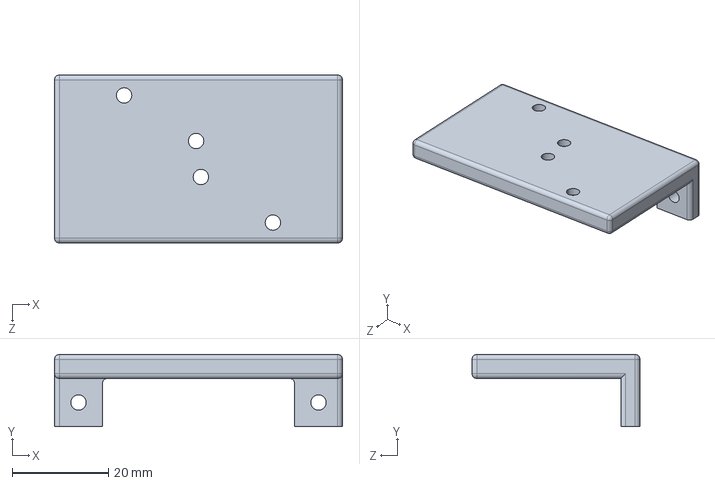
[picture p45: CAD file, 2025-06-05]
Mechanical/Production/3DP/Dual Head/阀支架.STEP
60.0 x 15.0 x 35.0 mm

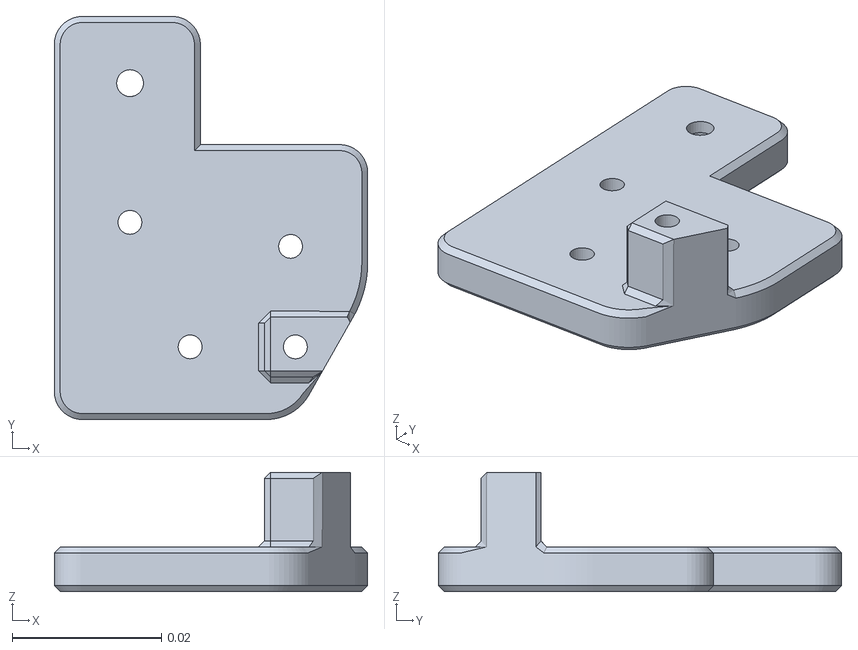
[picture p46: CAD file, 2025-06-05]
Mechanical/Production/3DP/SMT-Machine/Y臂左下.stl
0.042 x 0.054 x 0.016

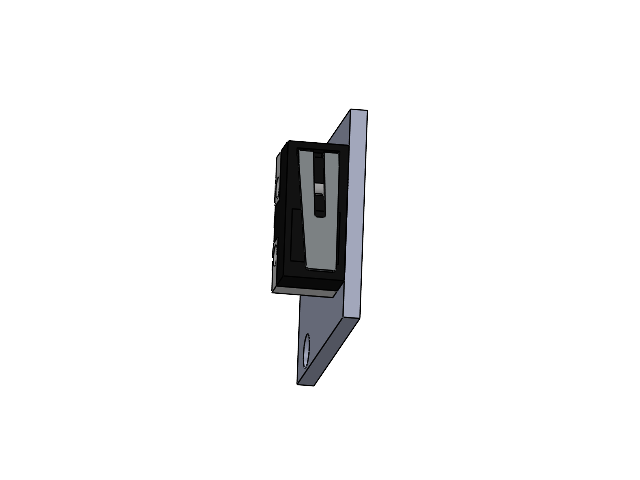
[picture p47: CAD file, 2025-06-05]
Mechanical/short-lever-micro-switch/Microsassem.SLDASM
Micro Switch
Lever
零件3^Microsassem

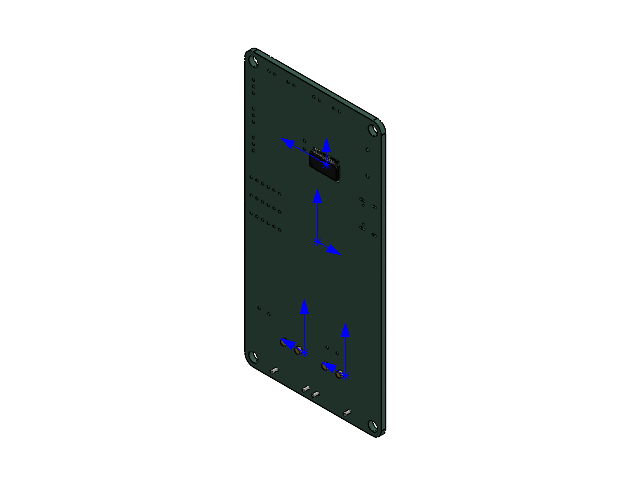
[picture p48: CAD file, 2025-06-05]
Mechanical/板支架/ELEC3300_SMT_Control_Board.SLDASM
HTSSOP_28_1EP_44x97mm_P065mm
Amass_XT30PW-M_pcb solder-0 x 2
ELEC3300_SMT_Control_Board_PCB

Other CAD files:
Mechanical/板支架/Amass_XT30PW-M_pcb solder.SLDASM
Mechanical/Feeder.SLDASM
Mechanical/Production/铝型材/Al.dwg
Mechanical/板支架/HTSSOP_28_1EP_44x97mm_P065mm.SLDPRT
Mechanical/0603_ComponentHolderType.SLDPRT
Mechanical/2020铝管.SLDPRT
Mechanical/28步进电机.SLDPRT
Mechanical/CAM Holder.SLDPRT
Mechanical/Home_Switch.SLDPRT
Mechanical/ITR1100.SLDPRT
Mechanical/M2_1.5垫片.SLDPRT
Mechanical/MGN12C_With_Rail.STEP
Mechanical/MotorHolderL.SLDPRT
Mechanical/OV2640_21mm-160_camera.STEP
Mechanical/PickerBoard.SLDPRT
Mechanical/PickerBoardIsolation.SLDPRT
Mechanical/PickerBoard_step.SLDPRT
Mechanical/Production/3DP/Dual Head/CAM Holder.STEP
Mechanical/Production/3DP/Dual Head/M2_1.5垫片.STEP
Mechanical/Production/3DP/Dual Head/PickerBoardIsolation.STEP
Mechanical/Production/3DP/Dual Head/Z-3d.STEP
Mechanical/Production/3DP/Dual Head/拉簧Holder.STEP
Mechanical/Production/3DP/Dual Head/贴装头背板.STEP
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

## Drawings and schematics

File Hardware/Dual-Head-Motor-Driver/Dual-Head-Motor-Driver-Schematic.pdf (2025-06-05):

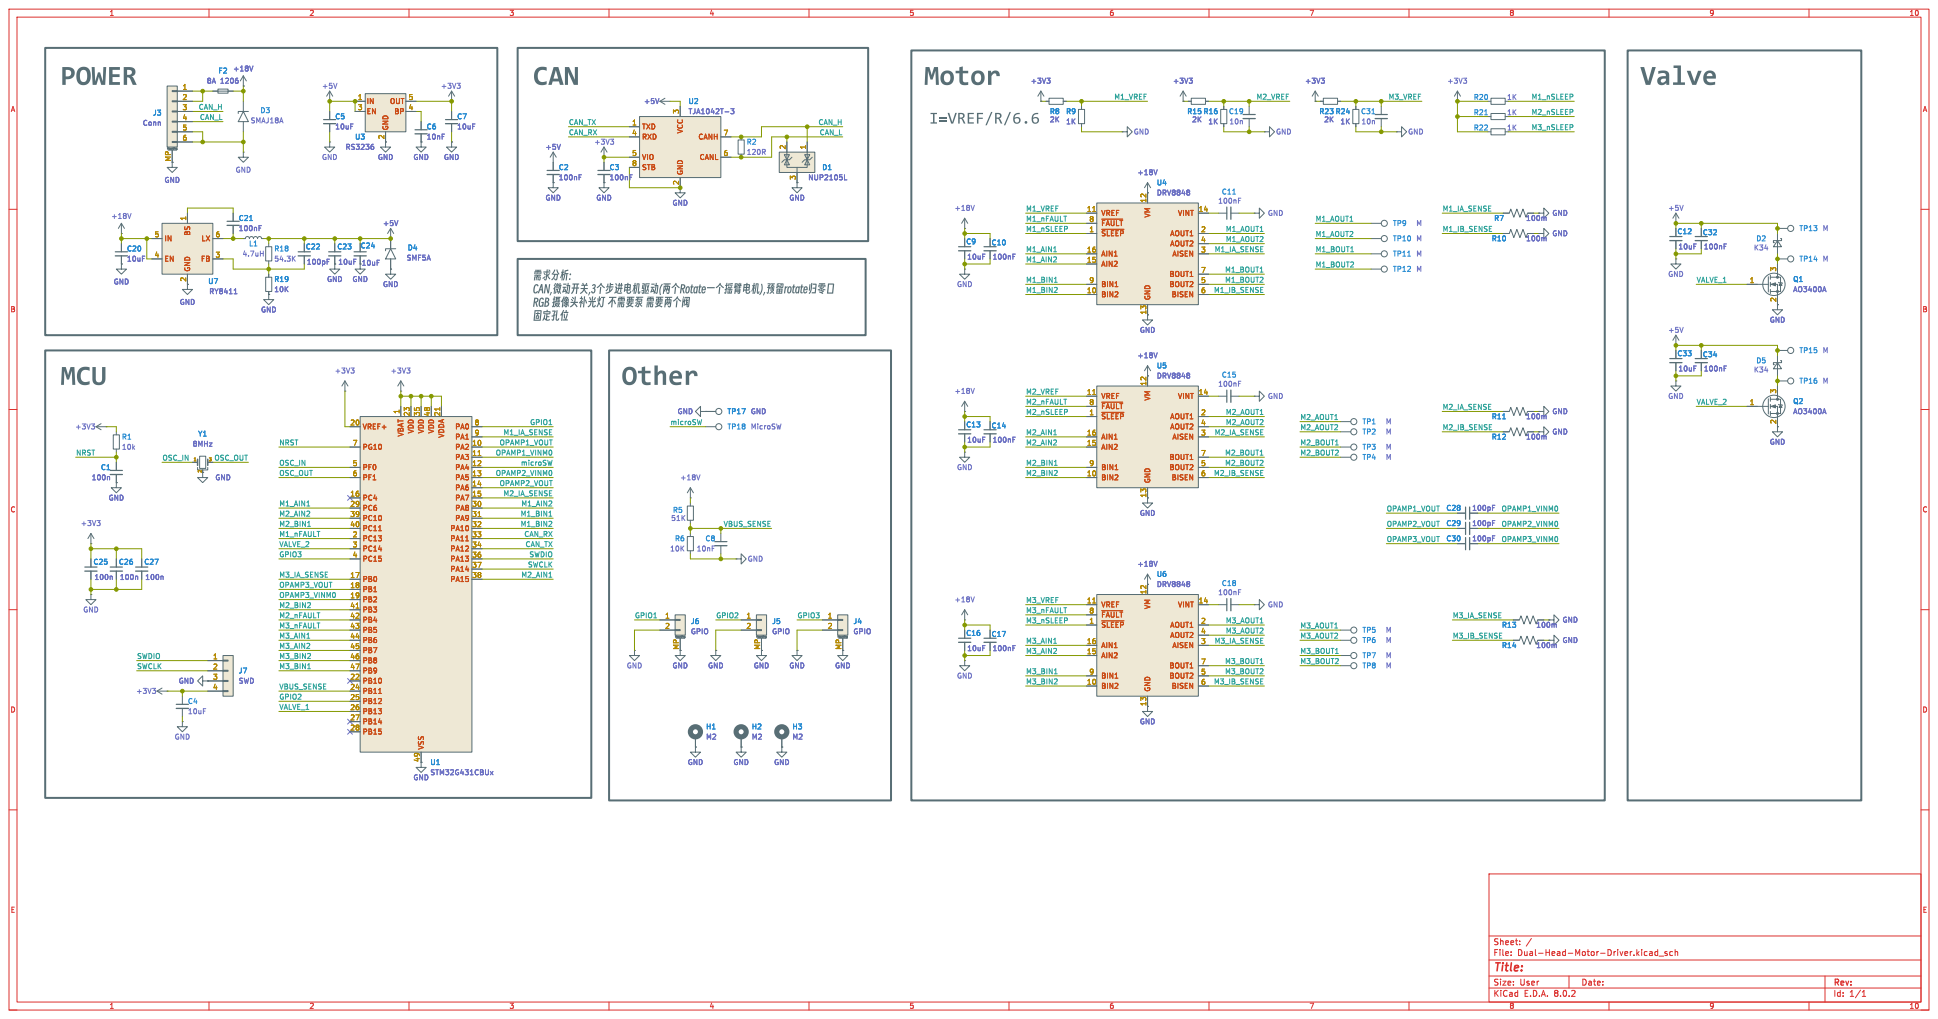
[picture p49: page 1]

2 EN 3 BP 4 OUT 5 U3 RS3236 GND

3 RXD 4 VIO 5 CANL 6 CANH 7 STB 8 U2 TJA1042T-3 R2

3 RXD 4 VIO 5 CANL 6 CANH 7 STB 8 GND

þÿCAN,_®R¨_Qs,3N*ke•Ûu5g:šqR¨(N$N*RotateNN*dG•Âu5g:),˜„uYrotate_R–öSã
RGBþÿdDPÏY4ˆeQIpo þÿN
þÿVú[š[TOM
Other
TP17 GND GND
TP18 MicroSW

1 PA2 10 PA3 11 PA4 12 PA5 13 PA6 14 PA7 15 PC4 16 PB0 17 PB1 18 PB2 19 PC13 2 VREF+ 20 VDDA 21 PB10 22 VDD 23 PB11 24 PB12 25 PB13 26 PB14 27 PB15 28 PC6 29 PC14 3 PA8 30 PA9 31 PA10 32 PA11 33 PA12 34 VDD 35 PA13 36 PA14 37 PA15 38 PC10 39 PC15 4 PC11 40 PB3 41 PB4 42 PB5 43 PB6 44 PB7 45 PB8 46 PB9 47 VDD 48 VSS 49 PF0 5 PF1 6 PG10 7 PA0 8 PA1 9 GND
8MHz

1 PA2 10 PA3 11 PA4 12 PA5 13 PA6 14 PA7 15 PC4 16 PB0 17 PB1 18 PB2 19 PC13 2 VREF+ 20 VDDA 21 PB10 22 VDD 23 PB11 24 PB12 25 PB13 26 PB14 27 PB15 28 PC6 29 PC14 3 PA8 30 PA9 31 PA10 32 PA11 33 PA12 34 VDD 35 PA13 36 PA14 37 PA15 38 PC10 39 PC15 4 PC11 40 PB3 41 PB4 42 PB5 43 PB6 44 PB7 45 PB8 46 PB9 47 VDD 48 VSS 49 PF0 5 PF1 6 PG10 7 PA0 8 PA1 9 U1STM32G431CBUx

GND GND

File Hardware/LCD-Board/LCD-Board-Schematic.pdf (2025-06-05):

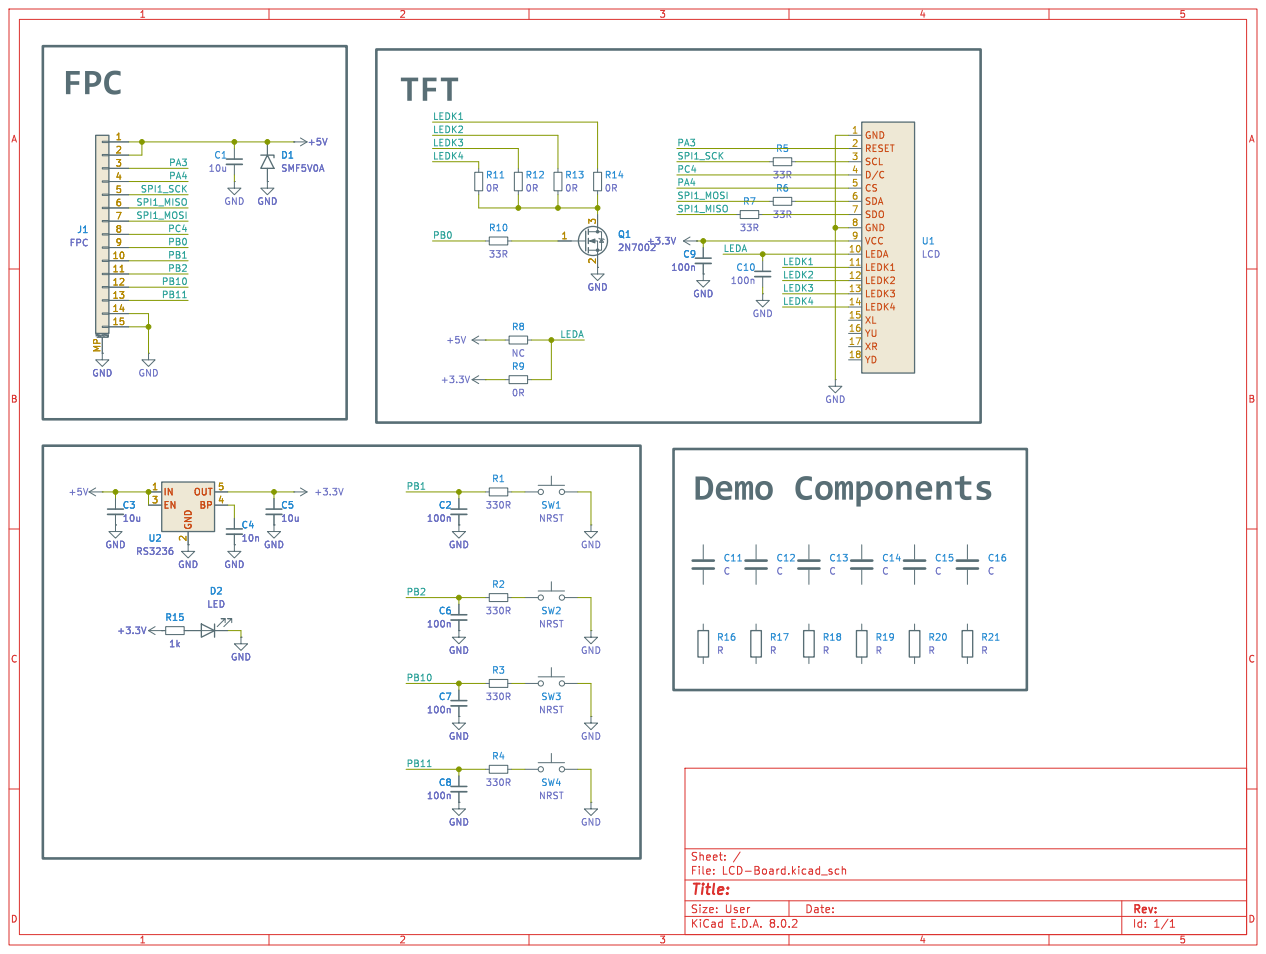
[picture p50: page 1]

2 EN 3 BP 4 OUT 5 U2 RS3236 +5V GND

2 EN 3 BP 4 OUT 5 GND

Id: 1/1 Title: File: LCD-Board.kicad_sch Sheet: /

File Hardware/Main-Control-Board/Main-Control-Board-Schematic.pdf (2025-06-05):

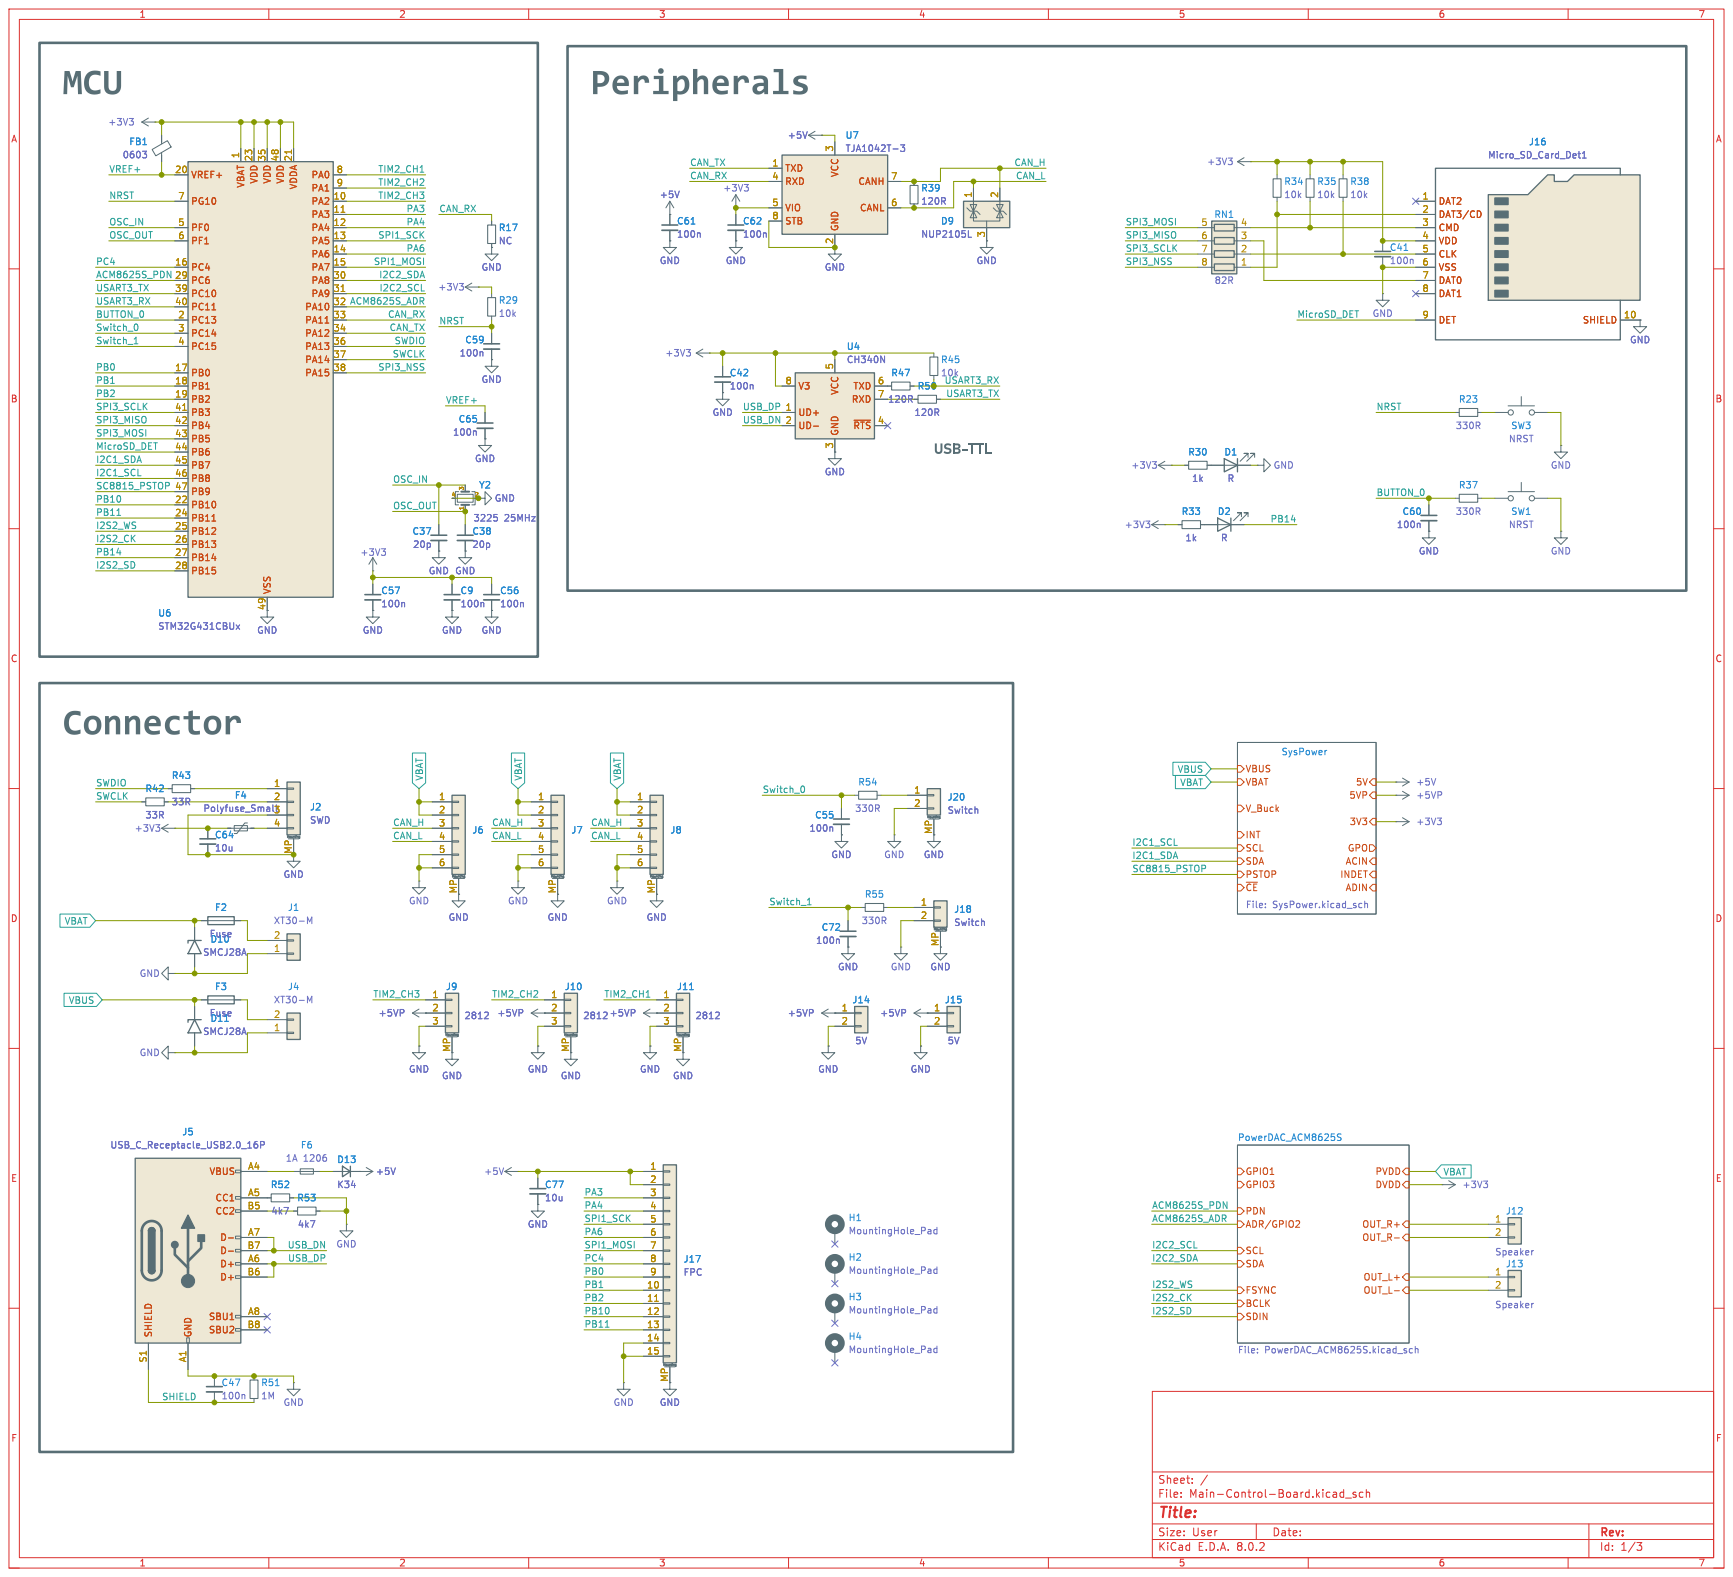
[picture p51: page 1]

1 PA2 10 PA3 11 PA4 12 PA5 13 PA6 14 PA7 15 PC4 16 PB0 17 PB1 18 PB2 19 PC13 2 VREF+ 20 VDDA 21 PB10 22 VDD 23 PB11 24 PB12 25 PB13 26 PB14 27 PB15 28 PC6 29 PC14 3 PA8 30 PA9 31 PA10 32 PA11 33 PA12 34 VDD 35 PA13 36 PA14 37 PA15 38 PC10 39 PC15 4 PC11 40 PB3 41 PB4 42 PB5 43 PB6 44 PB7 45 PB8 46 PB9 47 VDD 48 VSS 49 PF0 5 PF1 6 PG10 7 PA0 8 PA1 9 U6STM32G431CBUx +3V3 GND

1 PA2 10 PA3 11 PA4 12 PA5 13 PA6 14 PA7 15 PC4 16 PB0 17 PB1 18 PB2 19 PC13 2 VREF+ 20 VDDA 21 PB10 22 VDD 23 PB11 24 PB12 25 PB13 26 PB14 27 PB15 28 PC6 29 PC14 3 PA8 30 PA9 31 PA10 32 PA11 33 PA12 34 VDD 35 PA13 36 PA14 37 PA15 38 PC10 39 PC15 4 PC11 40 PB3 41 PB4 42 PB5 43 PB6 44 PB7 45 PB8 46 PB9 47 VDD 48 VSS 49 PF0 5 PF1 6 PG10 7 PA0 8 PA1 9 GND

3 RXD 4 VIO 5 CANL 6 CANH 7 STB 8 GND

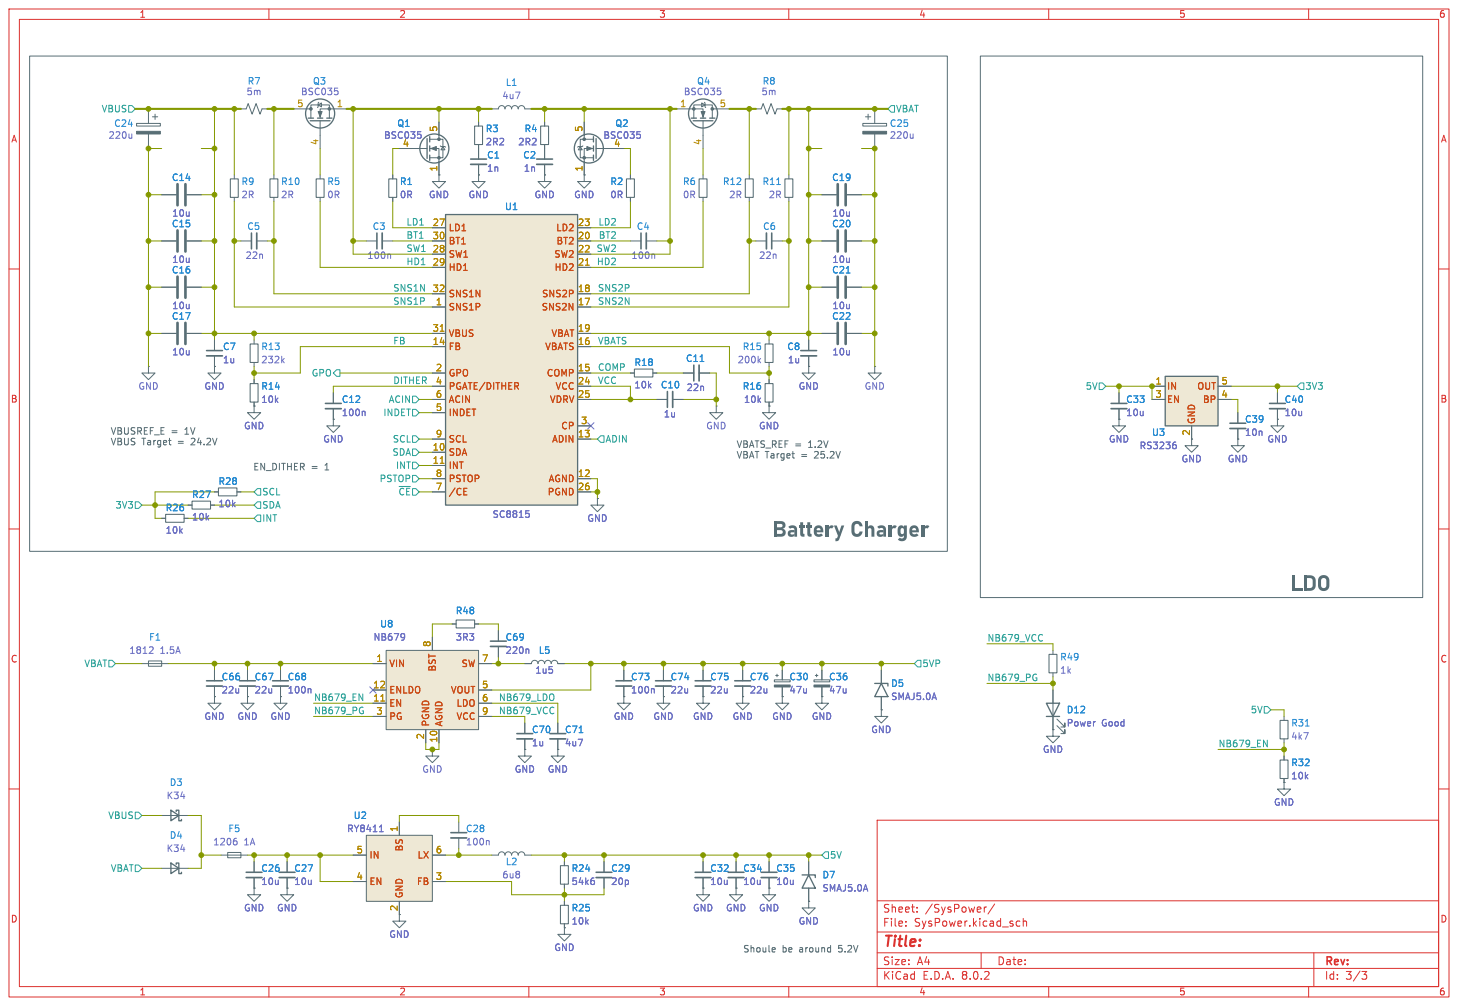
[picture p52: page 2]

2 EN 3 BP 4 OUT 5 GND
Shoule be around 5.2V BatteryCharger

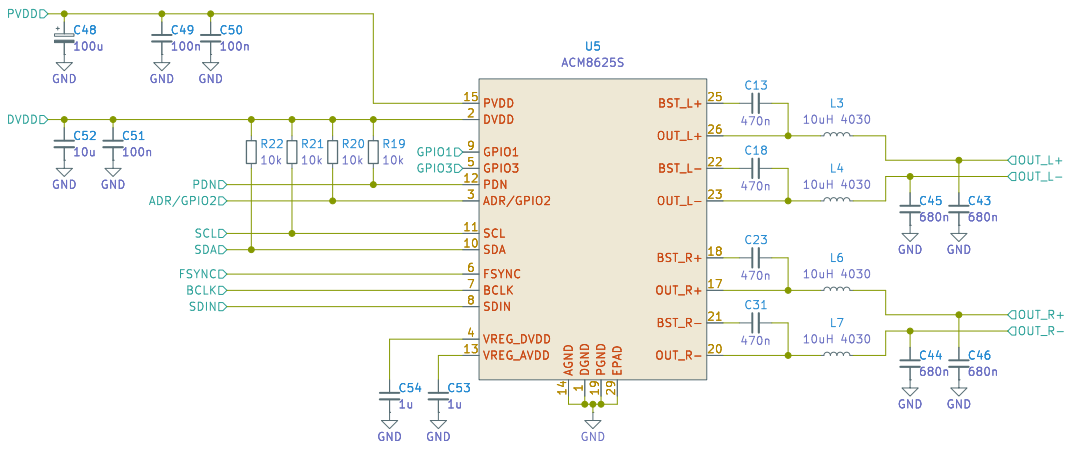
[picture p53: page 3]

1 SDA 10 SCL 11 PDN 12 VREG_AVDD 13 AGND 14 PVDD 15 OUT_R+ 17 BST_R+ 18 PGND 19 DVDD 2 OUT_R- 20 BST_R- 21 BST_L- 22 OUT_L- 23 BST_L+ 25 OUT_L+ 26 EPAD 29 ADR/GPIO2 3 VREG_DVDD 4 GPIO3 5 FSYNC 6 SDIN 8 GPIO1 9 BCLK 7 U5 ACM8625S C31

1 SDA 10 SCL 11 PDN 12 VREG_AVDD 13 AGND 14 PVDD 15 OUT_R+ 17 BST_R+ 18 PGND 19 DVDD 2 OUT_R- 20 BST_R- 21 BST_L- 22 OUT_L- 23 BST_L+ 25 OUT_L+ 26 EPAD 29 ADR/GPIO2 3 VREG_DVDD 4 GPIO3 5 FSYNC 6 SDIN 8 GPIO1 9 BCLK 7 C44

Id: 3/3 Title: File: PowerDAC_ACM8625S.kicad_sch Sheet: /PowerDAC_ACM8625S/

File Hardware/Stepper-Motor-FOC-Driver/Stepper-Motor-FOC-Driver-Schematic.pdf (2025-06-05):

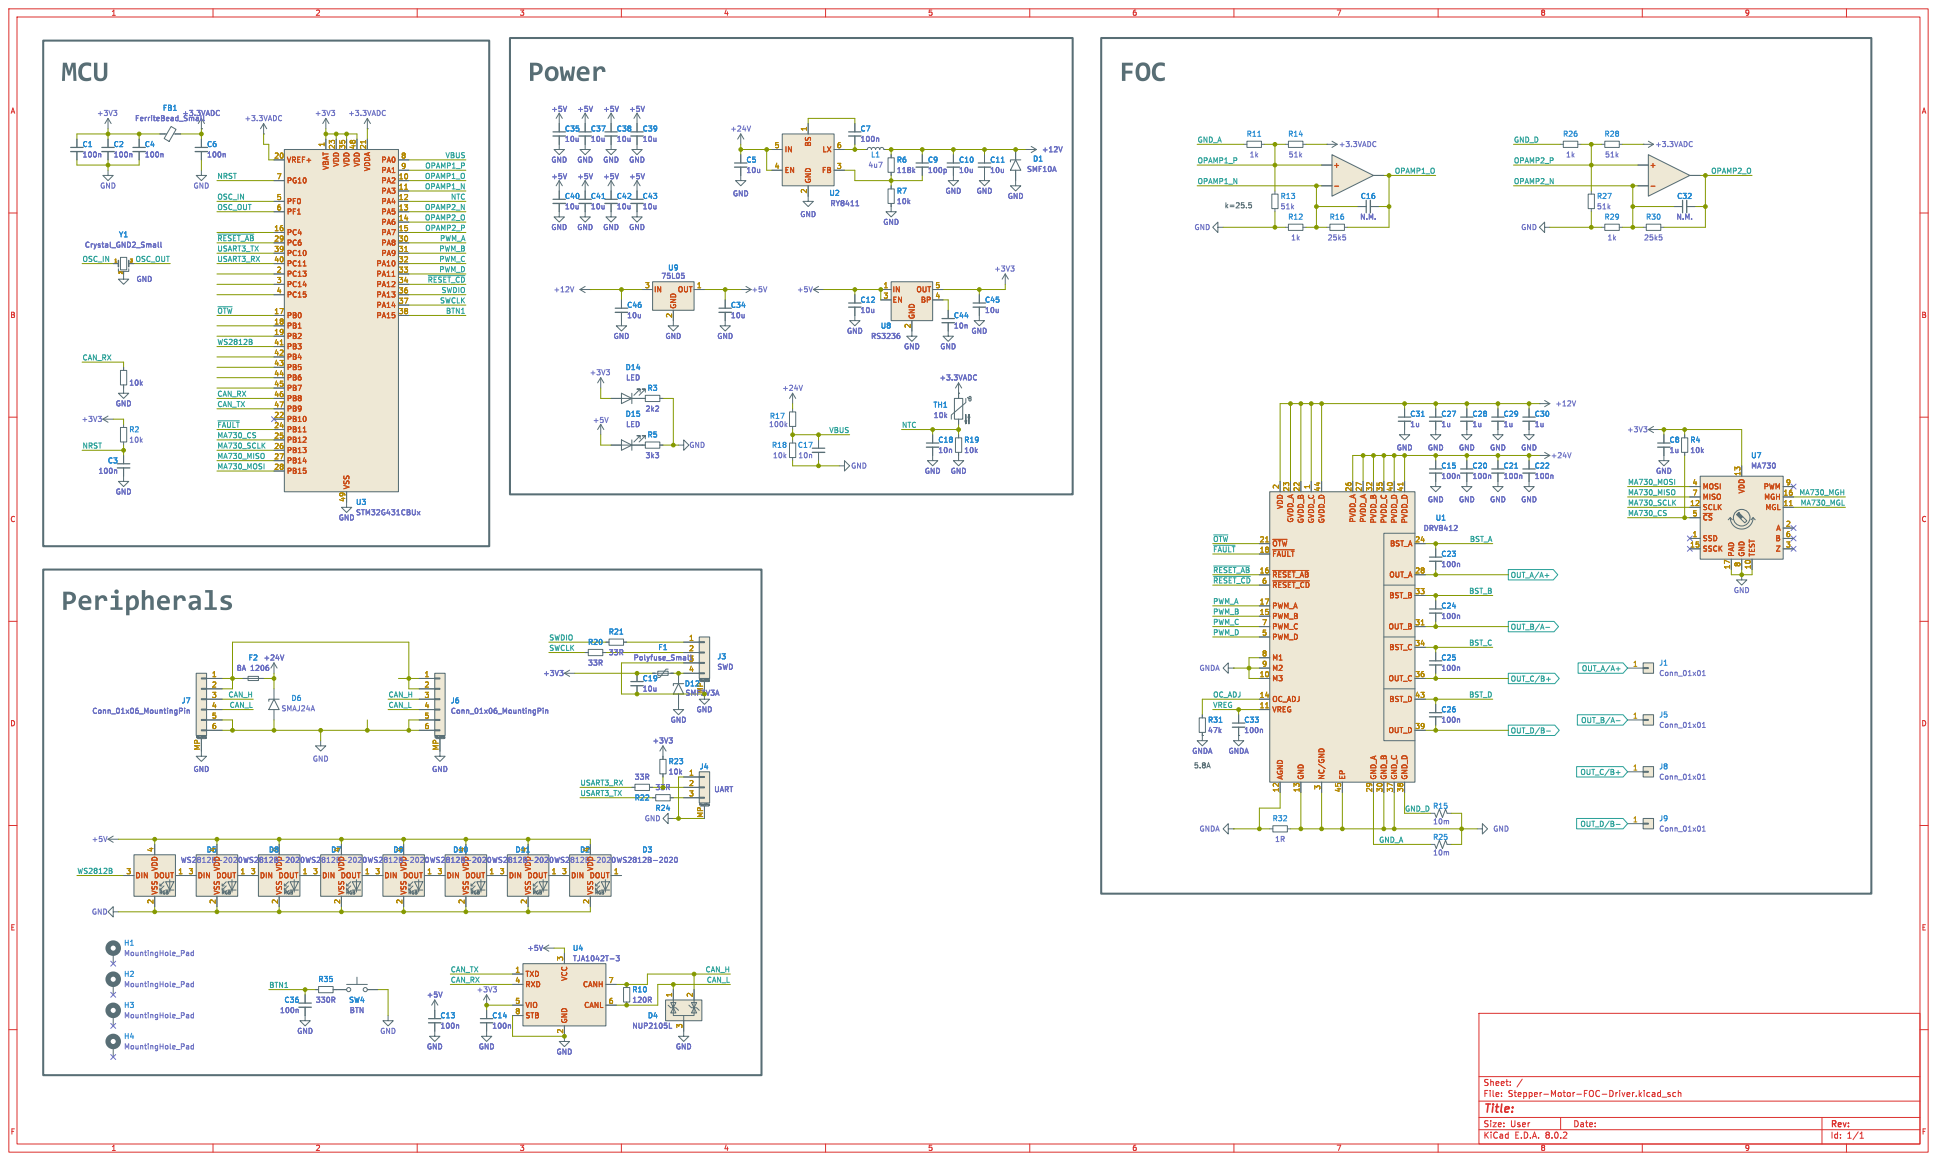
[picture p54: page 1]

1 PA2 10 PA3 11 PA4 12 PA5 13 PA6 14 PA7 15 PC4 16 PB0 17 PB1 18 PB2 19 PC13 2 VREF+ 20 VDDA 21 PB10 22 VDD 23 PB11 24 PB12 25 PB13 26 PB14 27 PB15 28 PC6 29 PC14 3 PA8 30 PA9 31 PA10 32 PA11 33 PA12 34 VDD 35 PA13 36 PA14 37 PA15 38 PC10 39 PC15 4 PC11 40 PB3 41 PB4 42 PB5 43 PB6 44 PB7 45 PB8 46 PB9 47 VDD 48 VSS 49 PF0 5 PF1 6 PG10 7 PA0 8 PA1 9 FB1 FerriteBead_Small +3.3VADC

1 PA2 10 PA3 11 PA4 12 PA5 13 PA6 14 PA7 15 PC4 16 PB0 17 PB1 18 PB2 19 PC13 2 VREF+ 20 VDDA 21 PB10 22 VDD 23 PB11 24 PB12 25 PB13 26 PB14 27 PB15 28 PC6 29 PC14 3 PA8 30 PA9 31 PA10 32 PA11 33 PA12 34 VDD 35 PA13 36 PA14 37 PA15 38 PC10 39 PC15 4 PC11 40 PB3 41 PB4 42 PB5 43 PB6 44 PB7 45 PB8 46 PB9 47 VDD 48 VSS 49 PF0 5 PF1 6 PG10 7 PA0 8 PA1 9 U3STM32G431CBUx GND

1 M3 10 VREG 11 AGND 12 GND 13 OC_ADJ 14 PWM_B 15 ~{RESET_AB} 16 PWM_A 17 ~{FAULT} 18 VDD

3 RXD 4 VIO 5 CANL 6 CANH 7 STB 8 U4 TJA1042T-3

3 RXD 4 VIO 5 CANL 6 CANH 7 STB 8 +5V R10

Id: 1/1 Title: File: Stepper-Motor-FOC-Driver.kicad_sch Sheet: /

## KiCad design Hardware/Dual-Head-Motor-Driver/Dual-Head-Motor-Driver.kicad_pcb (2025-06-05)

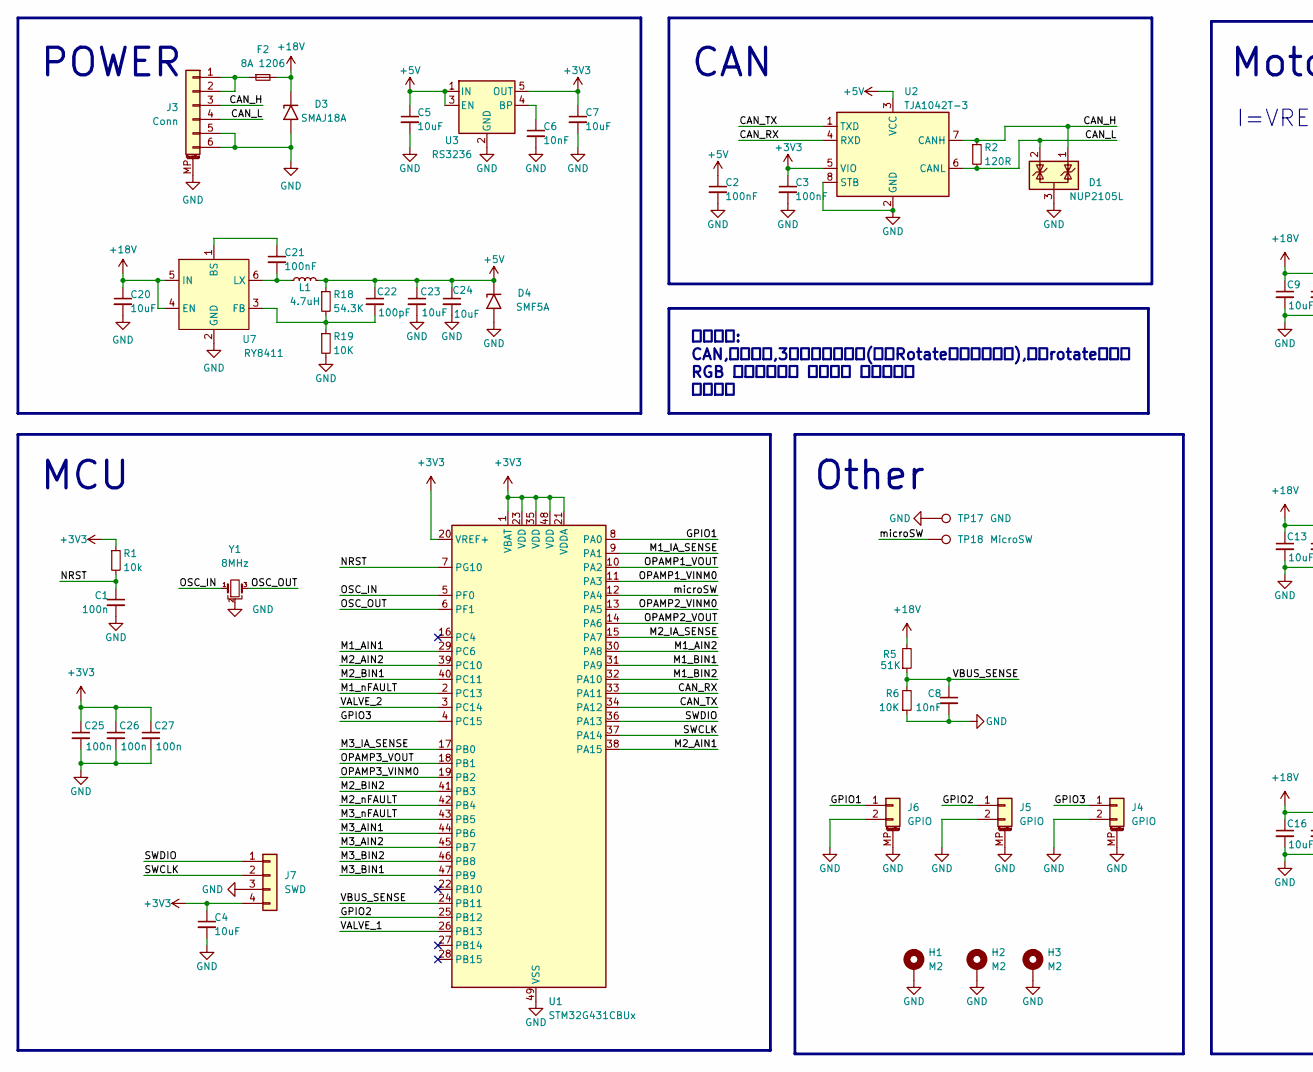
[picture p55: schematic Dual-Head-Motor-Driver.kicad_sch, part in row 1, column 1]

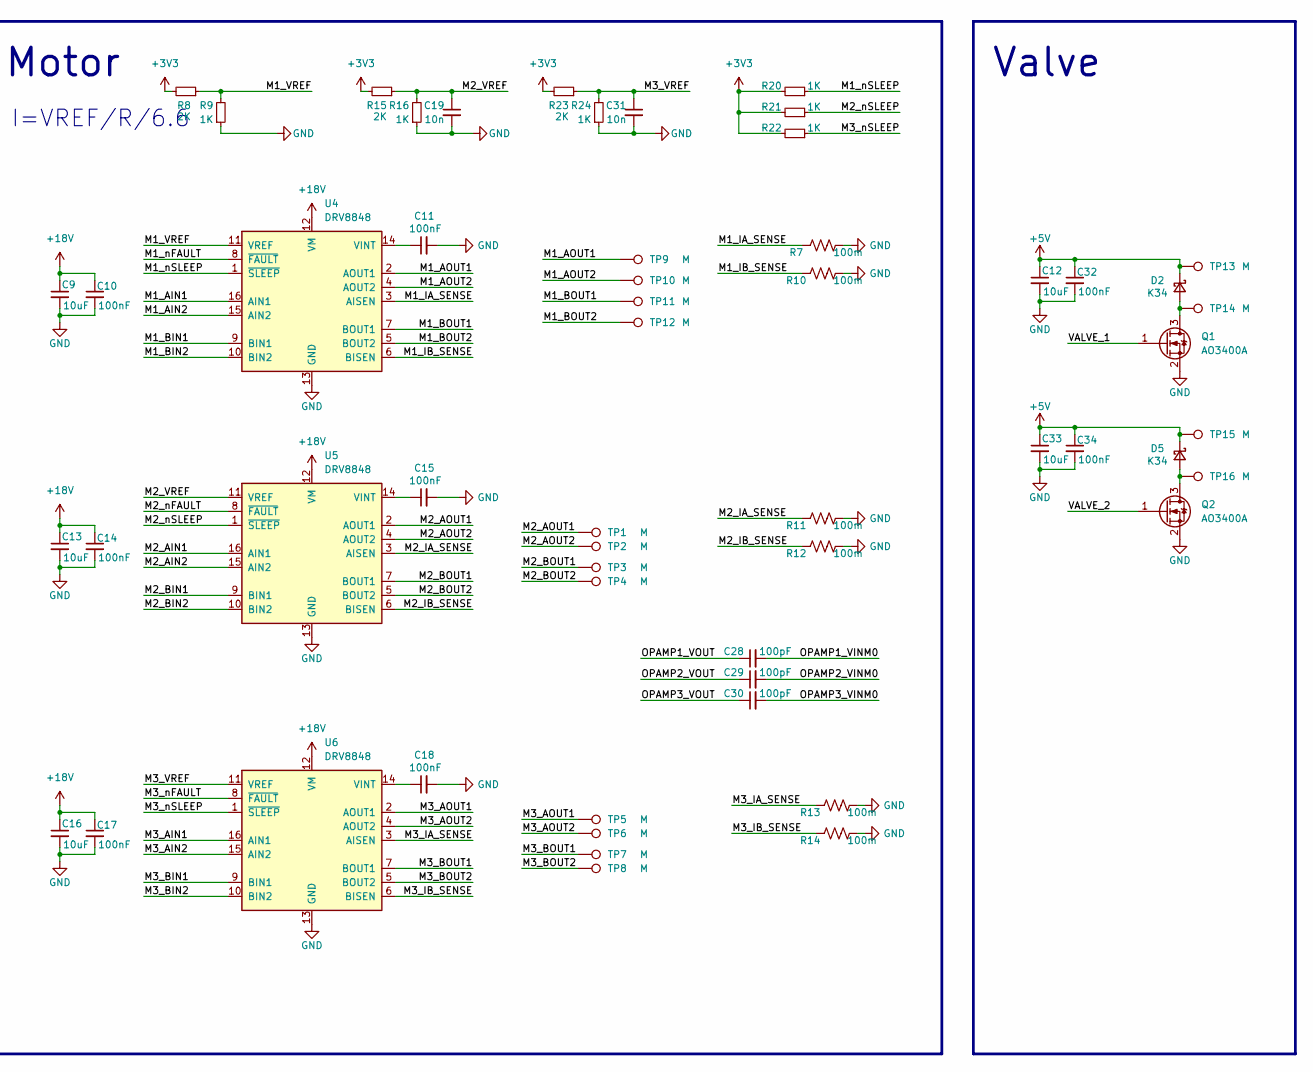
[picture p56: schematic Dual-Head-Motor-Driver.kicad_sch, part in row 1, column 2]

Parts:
C1, C25, C26, C27: 100n; C_0603_1608Metric
C2, C3, C10, C11, C14, C15, C17, C18, C21, C32, C34: 100nF; C_0603_1608Metric
C4, C5, C7: 10uF; C_0603_1608Metric
C6, C8: 10nF; C_0603_1608Metric
C9, C12, C13, C16, C20, C33: 10uF; C_1206_3216Metric
C19, C31: 10n; C_0603_1608Metric
C22, C28, C29, C30: 100pF; C_0603_1608Metric
C23, C24: 10uF; C_0805_2012Metric
D1: NUP2105L; SOT-23
D2, D5: K34; D_SMF
D3: SMAJ18A; D_SMA
D4: SMF5A; D_SMF
F2: 8A 1206; Fuse_1206_3216Metric
H1, H2, H3: M2; MountingHole_2.2mm_M2_Pad_Via
J3: Conn; JST_PH_B6B-PH-K_1x06_P2.00mm_Vertical
J4, J5: GPIO; JST_GH_SM02B-GHS-TB_1x02-1MP_P1.25mm_Horizontal
J6: GPIO; JST_GH_BM02B-GHS-TBT_1x02-1MP_P1.25mm_Vertical
J7: SWD; Molex_PicoBlade_53047-0410_1x04_P1.25mm_Vertical
L1: 4.7uH; L_Sunlord_SWPA3015S
Q1, Q2: AO3400A; SOT-23
R1: 10k; R_0603_1608Metric
R2: 120R; R_0603_1608Metric
R5: 51K; R_0603_1608Metric
R6, R19: 10K; R_0603_1608Metric
R7, R10, R11, R12, R13, R14: 100m; R_0805_2012Metric
R8, R15, R23: 2K; R_0603_1608Metric
R9, R16, R20, R21, R22, R24: 1K; R_0603_1608Metric
R18: 54.3K; R_0603_1608Metric
TP1, TP2, TP3, TP4, TP5, TP6, TP7, TP8, TP9, TP10, TP11, TP12, TP13, TP14, TP15, TP16: M; TestPoint_Pad_2.0x2.0mm
TP17: GND; TestPoint_Pad_2.0x2.0mm
TP18: MicroSW; TestPoint_Pad_2.0x2.0mm
U1: STM32G431CBUx; QFN-48-1EP_7x7mm_P0.5mm_EP5.6x5.6mm
U2: TJA1042T-3; SOIC-8_3.9x4.9mm_P1.27mm
U3: RS3236; SOT-23-5
U4, U5, U6: DRV8848; TSSOP-16-1EP_4.4x5mm_P0.65mm
U7: RY8411; SOT-23-6
Y1: 8MHz; Resonator_SMD_Murata_CSTxExxV-3Pin_3.0x1.1mm

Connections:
+3V3: C3.1, C4.1, C7.1, C25.1, C26.1, C27.1, J7.4, R1.1, R8.2, R15.2, R20.2, R21.2, R22.2, R23.2, U1.1 (VBAT), U1.20 (VREF+), U1.21 (VDDA), U1.23 (VDD), U1.35 (VDD), U1.48 (VDD), U2.5 (VIO), U3.5 (OUT)
+5V: C2.1, C5.1, C12.1, C22.1, C23.1, C24.1, C32.1, C33.1, C34.1, D2.1 (K), D4.1 (A1), D5.1 (K), L1.2, R18.1, TP13.1, TP15.1, U2.3 (VCC), U3.1 (IN), U3.3 (EN)
+18V: C9.1, C10.1, C13.1, C14.1, C16.1, C17.1, C20.1, D3.1 (A1), F2.2, R5.2, U4.12 (VM), U5.12 (VM), U6.12 (VM), U7.4 (EN), U7.5 (IN)
/CAN_H: D1.1 (K), J3.3, R2.1, U2.7 (CANH)
/CAN_L: D1.2 (K), J3.4, R2.2, U2.6 (CANL)
/CAN_RX: U1.33 (PA11), U2.4 (RXD)
/CAN_TX: U1.34 (PA12), U2.1 (TXD)
/GPIO1: J6.1, U1.8 (PA0)
/GPIO2: J5.1, U1.25 (PB12)
/GPIO3: J4.1, U1.4 (PC15)
/M1_AIN1: U1.29 (PC6), U4.16 (AIN1)
/M1_AIN2: U1.30 (PA8), U4.15 (AIN2)
/M1_AOUT1: TP9.1, U4.2 (AOUT1)
/M1_AOUT2: TP10.1, U4.4 (AOUT2)
/M1_BIN1: U1.31 (PA9), U4.9 (BIN1)
/M1_BIN2: U1.32 (PA10), U4.10 (BIN2)
/M1_BOUT1: TP11.1, U4.7 (BOUT1)
/M1_BOUT2: TP12.1, U4.5 (BOUT2)
/M1_IA_SENSE: R7.1, U1.9 (PA1), U4.3 (AISEN)
/M1_IB_SENSE: R10.1, U4.6 (BISEN)
/M1_VREF: R8.1, R9.2, U4.11 (VREF)
/M1_nFAULT: U1.2 (PC13), U4.8 (~FAULT)
/M1_nSLEEP: R20.1, U4.1 (~SLEEP)
/M2_AIN1: U1.38 (PA15), U5.16 (AIN1)
/M2_AIN2: U1.39 (PC10), U5.15 (AIN2)
/M2_AOUT1: TP1.1, U5.2 (AOUT1)
/M2_AOUT2: TP2.1, U5.4 (AOUT2)
/M2_BIN1: U1.40 (PC11), U5.9 (BIN1)
/M2_BIN2: U1.41 (PB3), U5.10 (BIN2)
/M2_BOUT1: TP3.1, U5.7 (BOUT1)
/M2_BOUT2: TP4.1, U5.5 (BOUT2)
/M2_IA_SENSE: R11.1, U1.15 (PA7), U5.3 (AISEN)
/M2_IB_SENSE: R12.1, U5.6 (BISEN)
/M2_VREF: C19.1, R15.1, R16.2, U5.11 (VREF)
/M2_nFAULT: U1.42 (PB4), U5.8 (~FAULT)
/M2_nSLEEP: R21.1, U5.1 (~SLEEP)
/M3_AIN1: U1.44 (PB6), U6.16 (AIN1)
/M3_AIN2: U1.45 (PB7), U6.15 (AIN2)
/M3_AOUT1: TP5.1, U6.2 (AOUT1)
/M3_AOUT2: TP6.1, U6.4 (AOUT2)
/M3_BIN1: U1.47 (PB9), U6.9 (BIN1)
/M3_BIN2: U1.46 (PB8), U6.10 (BIN2)
/M3_BOUT1: TP7.1, U6.7 (BOUT1)
/M3_BOUT2: TP8.1, U6.5 (BOUT2)
/M3_IA_SENSE: R13.1, U1.17 (PB0), U6.3 (AISEN)
/M3_IB_SENSE: R14.1, U6.6 (BISEN)
/M3_VREF: C31.1, R23.1, R24.2, U6.11 (VREF)
/M3_nFAULT: U1.43 (PB5), U6.8 (~FAULT)
/M3_nSLEEP: R22.1, U6.1 (~SLEEP)
/NRST: C1.1, R1.2, U1.7 (PG10)
/OPAMP1_VINM0: C28.2, U1.11 (PA3)
/OPAMP1_VOUT: C28.1, U1.10 (PA2)
/OPAMP2_VINM0: C29.2, U1.13 (PA5)
/OPAMP2_VOUT: C29.1, U1.14 (PA6)
/OPAMP3_VINM0: C30.2, U1.19 (PB2)
/OPAMP3_VOUT: C30.1, U1.18 (PB1)
/OSC_IN: U1.5 (PF0), Y1.1
/OSC_OUT: U1.6 (PF1), Y1.3
/SWCLK: J7.2, U1.37 (PA14)
/SWDIO: J7.1, U1.36 (PA13)
/VALVE_1: Q1.1 (G), U1.26 (PB13)
/VALVE_2: Q2.1 (G), U1.3 (PC14)
/VBUS_SENSE: C8.1, R5.1, R6.2, U1.24 (PB11)
/microSW: TP18.1, U1.12 (PA4)
GND: C1.2, C2.2, C3.2, C4.2, C5.2, C6.2, C7.2, C8.2, C9.2, C10.2, C11.2, C12.2, C13.2, C14.2, C15.2, C16.2, C17.2, C18.2, C19.2, C20.2, C23.2, C24.2, C25.2, C26.2, C27.2, C31.2, C32.2, C33.2, C34.2, D1.3 (A), D3.2 (A2), D4.2 (A2), H1.1, H2.1, H3.1, J3.5, J3.6, J3.MP (MountPin), J4.2, J4.MP (MountPin), J5.2, J5.MP (MountPin), J6.2, J6.MP (MountPin), J7.3, Q1.2 (S), Q2.2 (S), R6.1, R7.2, R9.1, R10.2, R11.2, R12.2, R13.2, R14.2, R16.1, R19.2, R24.1, TP17.1, U1.49 (VSS), U2.2 (GND), U2.8 (STB), U3.2 (GND), U4.13 (GND), U4.17 (GND), U5.13 (GND), U5.17 (GND), U6.13 (GND), U6.17 (GND), U7.2 (GND), Y1.2
unnamed: D2.2 (A), Q1.3 (D), TP14.1
unnamed: D5.2 (A), Q2.3 (D), TP16.1
unnamed: F2.1, J3.1, J3.2
unnamed: C6.1, U3.4 (BP)
unnamed: C11.1, U4.14 (VINT)
unnamed: C15.1, U5.14 (VINT)
unnamed: C18.1, U6.14 (VINT)
unnamed: C21.1, U7.1 (BS)
unnamed: C22.2, R18.2, R19.1, U7.3 (FB)
unnamed: C21.2, L1.1, U7.6 (LX)

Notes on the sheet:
需求分析: CAN,微动开关,3个步进电机驱动(两个Rotate一个摇臂电机),预留rotate归零口 RGB 摄像头补光灯 不需要泵 需要两个阀 固定孔位
CAN
Motor
Other
I=VREF/R/6.6
POWER
MCU
Valve

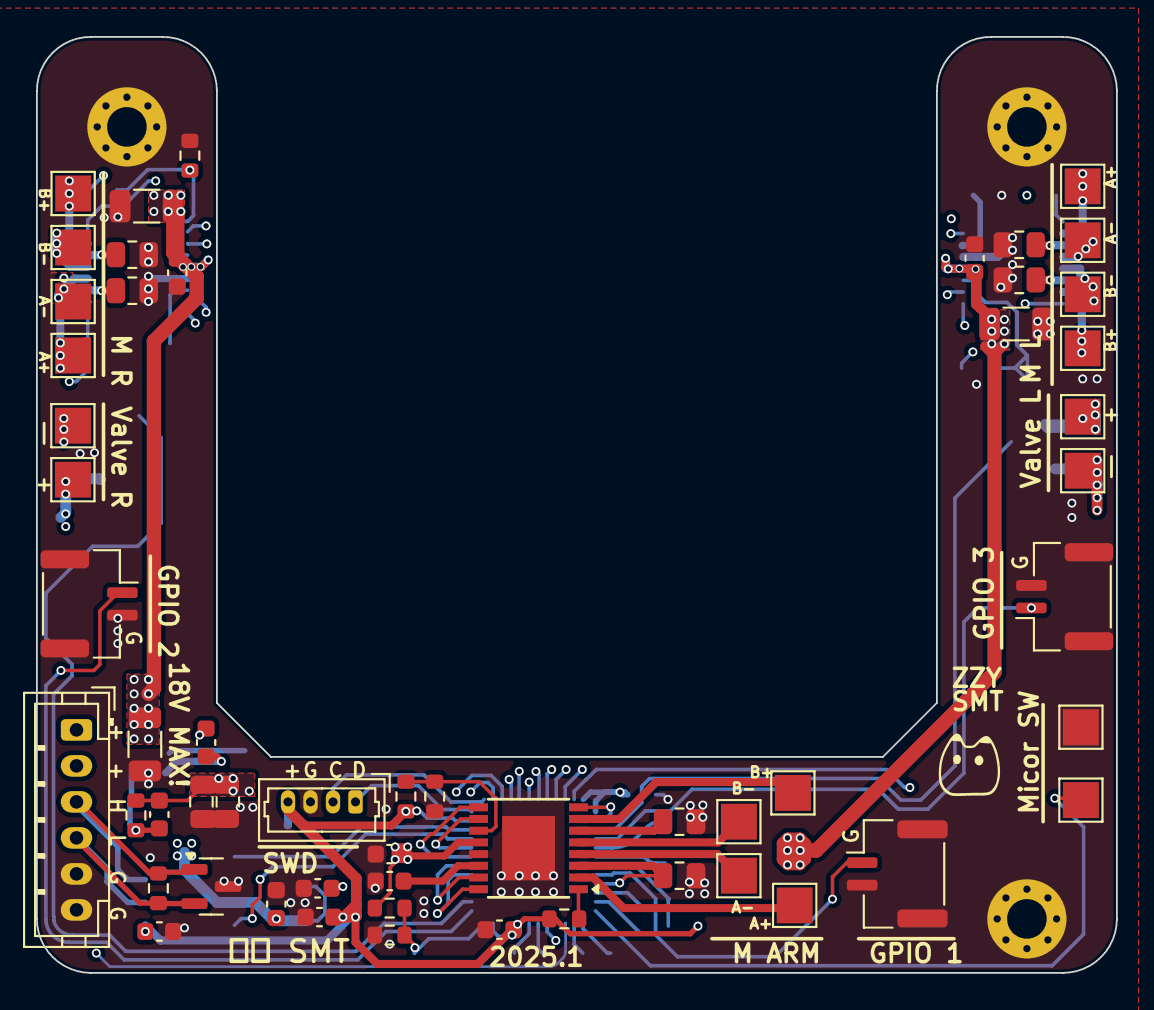
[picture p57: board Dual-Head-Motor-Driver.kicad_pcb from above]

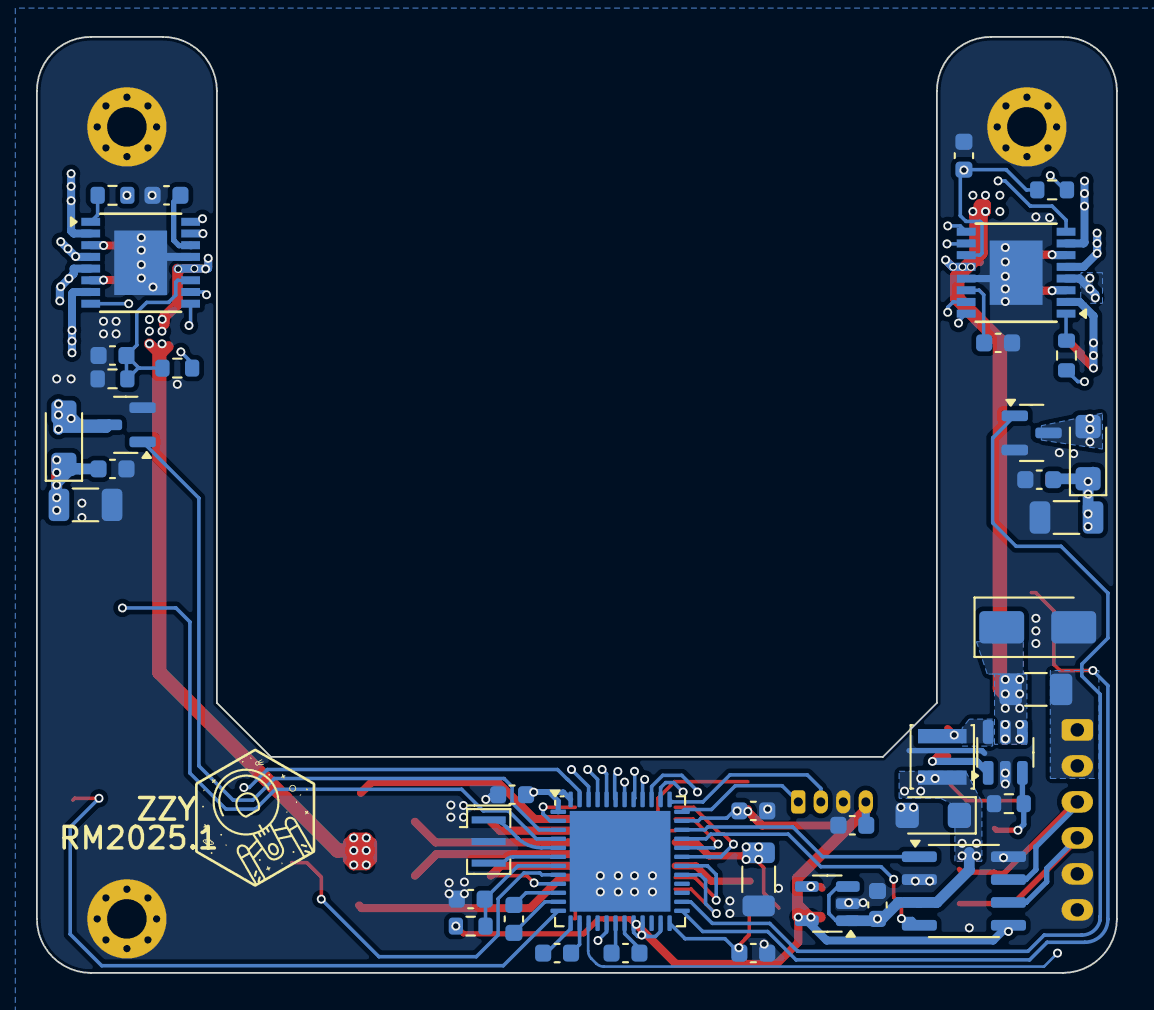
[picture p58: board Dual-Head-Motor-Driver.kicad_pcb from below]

Board: 4 copper layers, 60.0 x 52.0 mm, 98 parts (40 on the bottom side), 75 nets.

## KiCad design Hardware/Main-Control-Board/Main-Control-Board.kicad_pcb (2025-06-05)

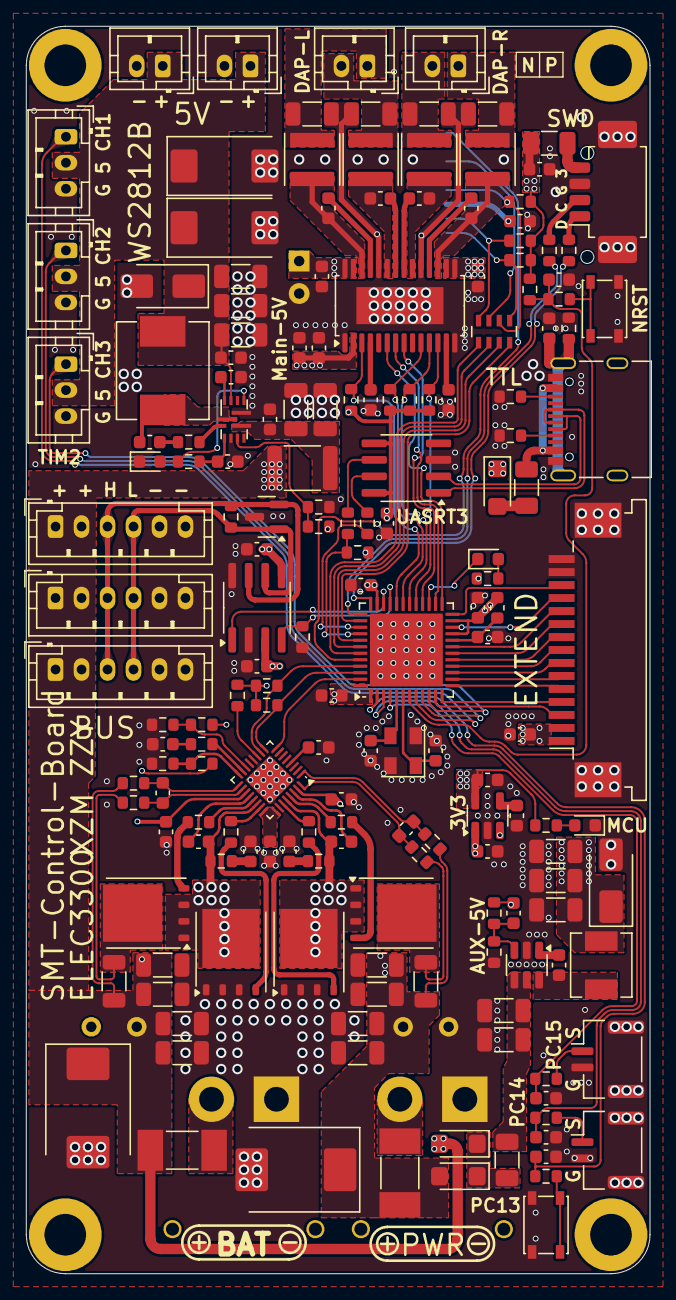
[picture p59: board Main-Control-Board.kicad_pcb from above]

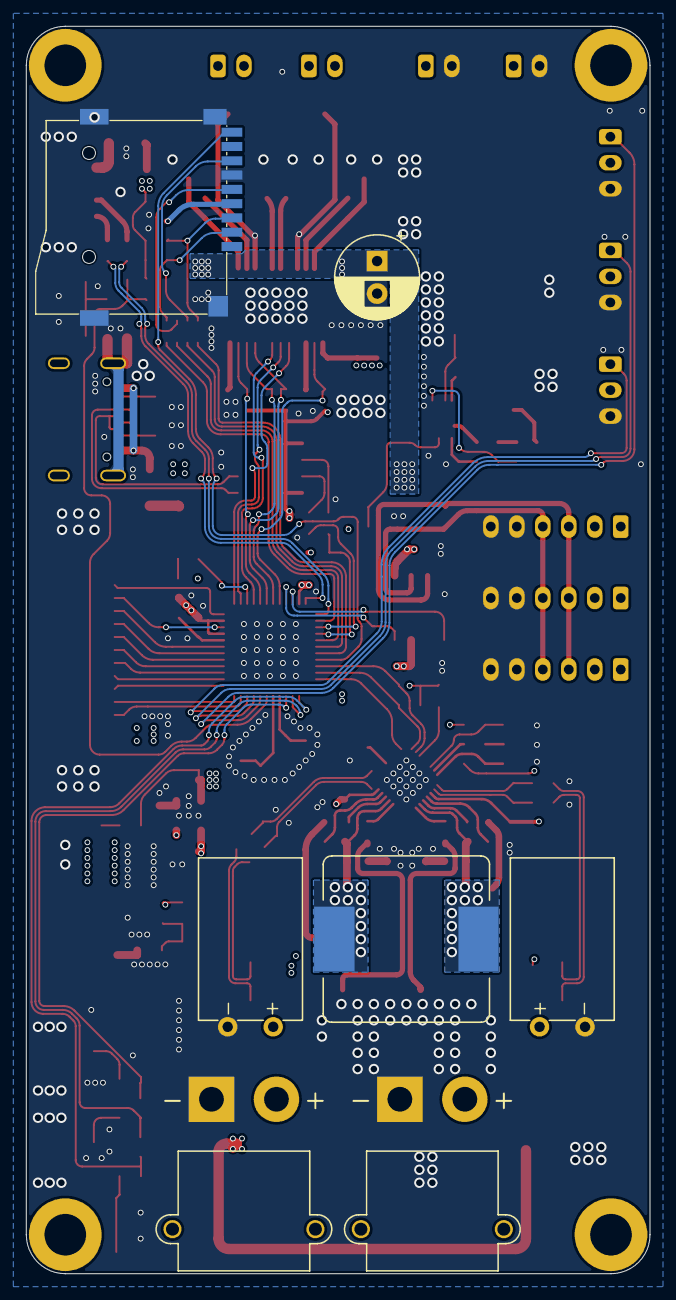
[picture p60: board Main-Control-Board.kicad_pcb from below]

Board: 4 copper layers, 48.0 x 96.0 mm, 188 parts (7 on the bottom side), 130 nets.

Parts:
C1, C2: 1n; C_0603_1608Metric
C3, C4, C9, C12, C28, C41, C42, C47, C49, C50, C51, C55, C56, C57, C59, C60, C61, C62, C65, C68, C72, C73: 100n; C_0603_1608Metric
C5, C6, C11: 22n; C_0603_1608Metric
C7, C8, C10, C53, C54, C70: 1u; C_0603_1608Metric
C13, C18, C23, C31: 470n; C_0603_1608Metric
C14, C15, C16, C17, C19, C20, C21, C22, C26, C27, C32, C34, C35: 10u; C_1206_3216Metric
C24: 220u; Cap_Al_D8xH12mm_Hor_Flip
C25: 220u; Cap_Al_D8xH12mm_Hor
C29, C37, C38: 20p; C_0603_1608Metric
C30, C36: 47u; CP_EIA-7343-15_Kemet-W
C33, C40, C52, C64, C77: 10u; C_0603_1608Metric
C39: 10n; C_0603_1608Metric
C43, C44, C45, C46: 680n; C_1206_3216Metric
C48: 100u; CP_Radial_D6.3mm_P2.50mm
C66, C67, C74, C75, C76: 22u; C_1206_3216Metric
C69: 220n; C_0603_1608Metric
C71: 4u7; C_0603_1608Metric
D1, D2: R; LED_0603_1608Metric
D3, D4, D13: K34; D_SMF
D5, D7: SMAJ5.0A; D_SMA
D9: NUP2105L; SOT-23
D10, D11: SMCJ28A; D_SMC
D12: Power Good; LED_0603_1608Metric
F1: 1812 1.5A; Fuse_1812_4532Metric
F2, F3: Fuse; Fuse_Littelfuse-NANO2-451_453
F4: Polyfuse_Small; Fuse_1206_3216Metric
F5: 1206 1A; Fuse_1206_3216Metric
F6: 1A 1206; Fuse_1206_3216Metric
FB1: 0603; L_0603_1608Metric
H1, H2, H3, H4: MountingHole_Pad; MountingHole_3.2mm_M3_DIN965_Pad
J1, J4: XT30-M; AMASS_XT30PW-M_1x02_P2.50mm_Horizontal
J2: SWD; Molex_PicoBlade_53261-0471_1x04-1MP_P1.25mm_Horizontal
J5: USB_C_Receptacle_USB2.0_16P; USB_C_Receptacle_Palconn_UTC16-G
J6, J7, J8: Conn_01x06_MountingPin; JST_PH_B6B-PH-K_1x06_P2.00mm_Vertical
J9, J10, J11: 2812; JST_PH_B3B-PH-K_1x03_P2.00mm_Vertical
J12, J13: Speaker; JST_PH_B2B-PH-K_1x02_P2.00mm_Vertical
J14, J15: 5V; JST_PH_B2B-PH-K_1x02_P2.00mm_Vertical
J16: Micro_SD_Card_Det1; Card XDFP-0090-012
J17: Conn_01x15_MountingPin; TE_1-84952-5_1x15-1MP_P1.0mm_Horizontal
J18, J20: Switch; JST_GH_BM02B-GHS-TBT_1x02-1MP_P1.25mm_Vertical
L1: 4u7; L_TaiTech_TMPC1265_13.5x12.5mm
L2: 6u8; L_Sunlord_MWSA0402S
L3, L4, L6, L7: 10uH 4030; L_Abracon_ASPI-4030S
L5: 1u5; L_Sunlord_MWSA0603S
Q1, Q2, Q3, Q4: BSC035; TDSON-8-1
R1, R2, R5, R6: 0R; R_0603_1608Metric
R3, R4: 2R2; R_0603_1608Metric
R7, R8: 5m; R_1206_3216Metric
R9, R10, R11, R12: 2R; R_0603_1608Metric
R13: 232k; R_0603_1608Metric
R14, R16, R18, R19, R20, R21, R22, R25, R26, R27, R28, R29, R32, R34, R35, R38, R45: 10k; R_0603_1608Metric
R15: 200k; R_0603_1608Metric
R17: NC; R_0603_1608Metric
R23, R37, R54, R55: 330R; R_0603_1608Metric
R24: 54k6; R_0603_1608Metric
R30, R33, R49: 1k; R_0603_1608Metric
R31, R52, R53: 4k7; R_0603_1608Metric
R39, R47, R50: 120R; R_0603_1608Metric
R42, R43: 33R; R_0603_1608Metric
R48: 3R3; R_0603_1608Metric
R51: 1M; R_0603_1608Metric
RN1: 82R; R_Array_Concave_4x0603
SW1, SW3: NRST; SW_SPST_PTS810
U1: SC8815; QFN-32-1EP_4x4mm_P0.4mm_EP2.65x2.65mm
U2: RY8411; SOT-23-6
U3: RS3236; SOT-23-5
U4: CH340N; SOIC-8_3.9x4.9mm_P1.27mm
U5: ACM8625S; TSSOP-28-1EP_4.4x9.7mm_P0.65mm_EP2.85x6.7mm
U6: STM32G431CBUx; QFN-48-1EP_7x7mm_P0.5mm_EP5.6x5.6mm
U7: TJA1042T-3; SOIC-8_3.9x4.9mm_P1.27mm
U8: NB679; QFN-12 2x3mm (NB679)
Y2: 3225 25MHz; Crystal_SMD_3225-4Pin_3.2x2.5mm

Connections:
+3V3: C9.1, C40.1, C41.1, C42.1, C51.1, C52.1, C56.1, C57.1, C62.1, C64.1, F4.1, FB1.1, J16.4 (VDD), R19.2, R20.2, R21.2, R22.2, R26.1, R27.1, R28.1, R29.1, R30.1, R33.1, R34.2, R35.2, R38.2, R45.2, U3.5 (OUT), U4.5 (VCC), U4.8 (V3), U5.2 (DVDD), U6.1 (VBAT), U6.21 (VDDA), U6.23 (VDD), U6.35 (VDD), U6.48 (VDD), U7.5 (VIO)
+5V: C29.1, C32.1, C33.1, C34.1, C35.1, C61.1, C77.1, D7.1 (A1), D13.1 (K), J17.1, J17.2, L2.2, R24.1, R31.1, U3.1 (IN), U3.3 (EN), U7.3 (VCC)
+5VP: C30.1, C36.1, C73.1, C74.1, C75.1, C76.1, D5.1 (A1), J9.2, J10.2, J11.2, J14.1, J15.1, L5.2, U8.5 (VOUT)
/ACM8625S_ADR: R20.1, U5.3 (ADR/GPIO2), U6.32 (PA10)
/ACM8625S_PDN: R19.1, U5.12 (PDN), U6.29 (PC6)
/BUTTON_0: C60.1, R37.1, U6.2 (PC13)
/CAN_H: D9.2 (K), J6.3, J7.3, J8.3, R39.1, U7.7 (CANH)
/CAN_L: D9.1 (K), J6.4, J7.4, J8.4, R39.2, U7.6 (CANL)
/CAN_RX: R17.1, U6.33 (PA11), U7.4 (RXD)
/CAN_TX: U6.34 (PA12), U7.1 (TXD)
/I2C1_SCL: R28.2, U1.9 (SCL), U6.46 (PB8)
/I2C1_SDA: R27.2, U1.10 (SDA), U6.45 (PB7)
/I2C2_SCL: R21.1, U5.11 (SCL), U6.31 (PA9)
/I2C2_SDA: R22.1, U5.10 (SDA), U6.30 (PA8)
/I2S2_CK: U5.7 (BCLK), U6.26 (PB13)
/I2S2_SD: U5.8 (SDIN), U6.28 (PB15)
/I2S2_WS: U5.6 (FSYNC), U6.25 (PB12)
/MicroSD_DET: J16.9 (DET), U6.44 (PB6)
/NRST: C59.1, R23.1, R29.2, U6.7 (PG10)
/OSC_IN: C37.1, U6.5 (PF0), Y2.3
/OSC_OUT: C38.1, U6.6 (PF1), Y2.1
/PA3: J17.3, U6.11 (PA3)
/PA4: J17.4, U6.12 (PA4)
/PA6: J17.6, U6.14 (PA6)
/PB0: J17.9, U6.17 (PB0)
/PB1: J17.10, U6.18 (PB1)
/PB2: J17.11, U6.19 (PB2)
/PB10: J17.12, U6.22 (PB10)
/PB11: J17.13, U6.24 (PB11)
/PB14: D2.1 (K), U6.27 (PB14)
/PC4: J17.8, U6.16 (PC4)
/PowerDAC_ACM8625S/OUT_L+: C43.1, J13.1, L3.2
/PowerDAC_ACM8625S/OUT_L-: C45.1, J13.2, L4.2
/PowerDAC_ACM8625S/OUT_R+: C46.1, J12.1, L6.2
/PowerDAC_ACM8625S/OUT_R-: C44.1, J12.2, L7.2
/SC8815_PSTOP: U1.8 (PSTOP), U6.47 (PB9)
/SHIELD: C47.2, J5.S1 (SHIELD), R51.2
/SPI1_MOSI: J17.7, U6.15 (PA7)
/SPI1_SCK: J17.5, U6.13 (PA5)
/SPI3_MISO: RN1.6 (R3.2), U6.42 (PB4)
/SPI3_MOSI: RN1.5 (R4.2), U6.43 (PB5)
/SPI3_NSS: RN1.8 (R1.2), U6.38 (PA15)
/SPI3_SCLK: RN1.7 (R2.2), U6.41 (PB3)
/SWCLK: R42.1, U6.37 (PA14)
/SWDIO: R43.1, U6.36 (PA13)
/Switch_0: C55.1, R54.1, U6.3 (PC14)
/Switch_1: C72.1, R55.1, U6.4 (PC15)
/SysPower/BT1: C3.2, U1.30 (BT1)
/SysPower/BT2: C4.1, U1.20 (BT2)
/SysPower/COMP: R18.1, U1.15 (COMP)
/SysPower/DITHER: C12.1, U1.4 (PGATE/DITHER)
/SysPower/FB: R13.2, R14.1, U1.14 (FB)
/SysPower/HD1: R5.2, U1.29 (HD1)
/SysPower/HD2: R6.2, U1.21 (HD2)
/SysPower/INT: R26.2, U1.11 (INT)
/SysPower/LD1: R1.2, U1.27 (LD1)
/SysPower/LD2: R2.2, U1.23 (LD2)
/SysPower/NB679_EN: R31.2, R32.1, U8.11 (EN)
/SysPower/NB679_LDO: C71.1, U8.6 (LDO)
/SysPower/NB679_PG: D12.2 (A), R49.2, U8.3 (PG)
/SysPower/NB679_VCC: C70.1, R49.1, U8.9 (VCC)
/SysPower/SNS1N: C5.2, R10.2, U1.32 (SNS1N)
/SysPower/SNS1P: C5.1, R9.2, U1.1 (SNS1P)
/SysPower/SNS2N: C6.1, R11.2, U1.17 (SNS2N)
/SysPower/SNS2P: C6.2, R12.2, U1.18 (SNS2P)
/SysPower/SW1: C3.1, L1.2, Q1.5 (D), Q3.1 (S), Q3.2 (S), Q3.3 (S), R3.1, U1.28 (SW1)
/SysPower/SW2: C4.2, L1.1, Q2.5 (D), Q4.1 (S), Q4.2 (S), Q4.3 (S), R4.1, U1.22 (SW2)
/SysPower/VBATS: R15.2, R16.1, U1.16 (VBATS)
/SysPower/VCC: C10.1, U1.24 (VCC), U1.25 (VDRV)
/TIM2_CH1: J11.1, U6.8 (PA0)
/TIM2_CH2: J10.1, U6.9 (PA1)
/TIM2_CH3: J9.1, U6.10 (PA2)
/USART3_RX: R45.1, R47.2, U6.40 (PC11)
/USART3_TX: R50.2, U6.39 (PC10)
/USB_DN: J5.A7 (D-), J5.B7 (D-), U4.2 (UD-)
/USB_DP: J5.A6 (D+), J5.B6 (D+), U4.1 (UD+)
/VREF+: C65.1, FB1.2, U6.20 (VREF+)
GND: C1.2, C2.2, C7.2, C8.2, C9.2, C10.2, C11.2, C12.2, C14.1, C15.1, C16.1, C17.1, C19.2, C20.2, C21.2, C22.2, C24.2, C25.2, C26.2, C27.2, C30.2, C32.2, C33.2, C34.2, C35.2, C36.2, C37.2, C38.2, C39.2, C40.2, C41.2, C42.2, C43.2, C44.2, C45.2, C46.2, C47.1, C48.2, C49.2, C50.2, C51.2, C52.2, C53.2, C54.2, C55.2, C56.2, C57.2, C59.2, C60.2, C61.2, C62.2, C64.2, C65.2, C66.2, C67.2, C68.2, C70.2, C71.2, C72.2, C73.2, C74.2, C75.2, C76.2, C77.2, D1.1 (K), D5.2 (A2), D7.2 (A2), D9.3 (A), D10.2 (A2), D11.2 (A2), D12.1 (K), J1.1, J2.3, J2.MP (MountPin), J4.1, J5.A1 (GND), J5.A12 (GND), J5.B1 (GND), J5.B12 (GND), J6.5, J6.6, J7.5, J7.6, J8.5, J8.6, J9.3, J10.3, J11.3, J14.2, J15.2, J16.6 (VSS), J16.10 (SHIELD), J17.14, J17.15, J17.MP (MountPin), J18.2, J18.MP (MountPin), J20.2, J20.MP (MountPin), Q1.1 (S), Q1.2 (S), Q1.3 (S), Q2.1 (S), Q2.2 (S), Q2.3 (S), R14.2, R16.2, R17.2, R25.2, R32.2, R51.1, R52.2, R53.2, SW1.2, SW3.2, U1.12 (AGND), U1.26 (PGND), U1.33 (PGND), U2.2 (GND), U3.2 (GND), U4.3 (GND), U5.1 (DGND), U5.14 (AGND), U5.19 (PGND), U5.24 (PGND), U5.29 (EPAD), U6.49 (VSS), U7.2 (GND), U7.8 (STB), U8.2 (PGND), U8.10 (AGND), Y2.2, Y2.4
unnamed: C1.1, R3.2
unnamed: C2.1, R4.2
unnamed: C11.1, R18.2
unnamed: C69.1, R48.2
unnamed: D1.2 (A), R30.2
unnamed: D2.2 (A), R33.2
unnamed: D3.1 (K), D4.1 (K), F5.1
unnamed: D13.2 (A), F6.2
unnamed: F6.1, J5.A4 (VBUS), J5.A9 (VBUS), J5.B4 (VBUS), J5.B9 (VBUS)
unnamed: F2.2, J1.2
unnamed: J2.1, R43.2
unnamed: J2.2, R42.2
unnamed: F4.2, J2.4
unnamed: F3.2, J4.2
unnamed: J5.A5 (CC1), R52.1
unnamed: J5.B5 (CC2), R53.1
unnamed: J16.5 (CLK), R38.1, RN1.2 (R2.1)
unnamed: J16.3 (CMD), R35.1, RN1.4 (R4.1)
unnamed: J16.7 (DAT0), RN1.3 (R3.1)
unnamed: J16.2 (DAT3/CD), R34.1, RN1.1 (R1.1)
unnamed: J18.1, R55.2
unnamed: J20.1, R54.2
unnamed: Q1.4 (G), R1.1
unnamed: Q2.4 (G), R2.1
unnamed: Q3.5 (D), R7.2, R10.1
unnamed: Q3.4 (G), R5.1
unnamed: Q4.5 (D), R8.1, R12.1
unnamed: Q4.4 (G), R6.1
unnamed: R23.2, SW3.1
unnamed: R37.2, SW1.1
unnamed: C28.1, U2.1 (BS)
unnamed: C26.1, C27.1, F5.2, U2.4 (EN), U2.5 (IN)
unnamed: C29.2, R24.2, R25.1, U2.3 (FB)
unnamed: C28.2, L2.1, U2.6 (LX)
unnamed: C39.1, U3.4 (BP)
unnamed: R50.1, U4.7 (RXD)
unnamed: R47.1, U4.6 (TXD)
unnamed: C13.1, U5.25 (BST_L+)
unnamed: C18.1, U5.22 (BST_L-)
unnamed: C23.1, U5.18 (BST_R+)
unnamed: C31.1, U5.21 (BST_R-)
unnamed: C13.2, L3.1, U5.26 (OUT_L+)
unnamed: C18.2, L4.1, U5.23 (OUT_L-)
unnamed: C23.2, L6.1, U5.17 (OUT_R+)
unnamed: C31.2, L7.1, U5.20 (OUT_R-)
unnamed: C53.1, U5.13 (VREG_AVDD)
unnamed: C54.1, U5.4 (VREG_DVDD)
unnamed: R48.1, U8.8 (BST)
unnamed: C69.2, L5.1, U8.7 (SW)
unnamed: C66.1, C67.1, C68.1, F1.2, U8.1 (VIN)
VBAT: C8.1, C19.1, C20.1, C21.1, C22.1, C25.1, C48.1, C49.1, C50.1, D4.2 (A), D10.1 (A1), F1.1, F2.1, J6.1, J6.2, J7.1, J7.2, J8.1, J8.2, R8.2, R11.1, R15.1, U1.19 (VBAT), U5.15 (PVDD), U5.16 (PVDD), U5.27 (PVDD), U5.28 (PVDD)
VBUS: C7.1, C14.2, C15.2, C16.2, C17.2, C24.1, D3.2 (A), D11.1 (A1), F3.1, R7.1, R9.1, R13.1, U1.31 (VBUS)

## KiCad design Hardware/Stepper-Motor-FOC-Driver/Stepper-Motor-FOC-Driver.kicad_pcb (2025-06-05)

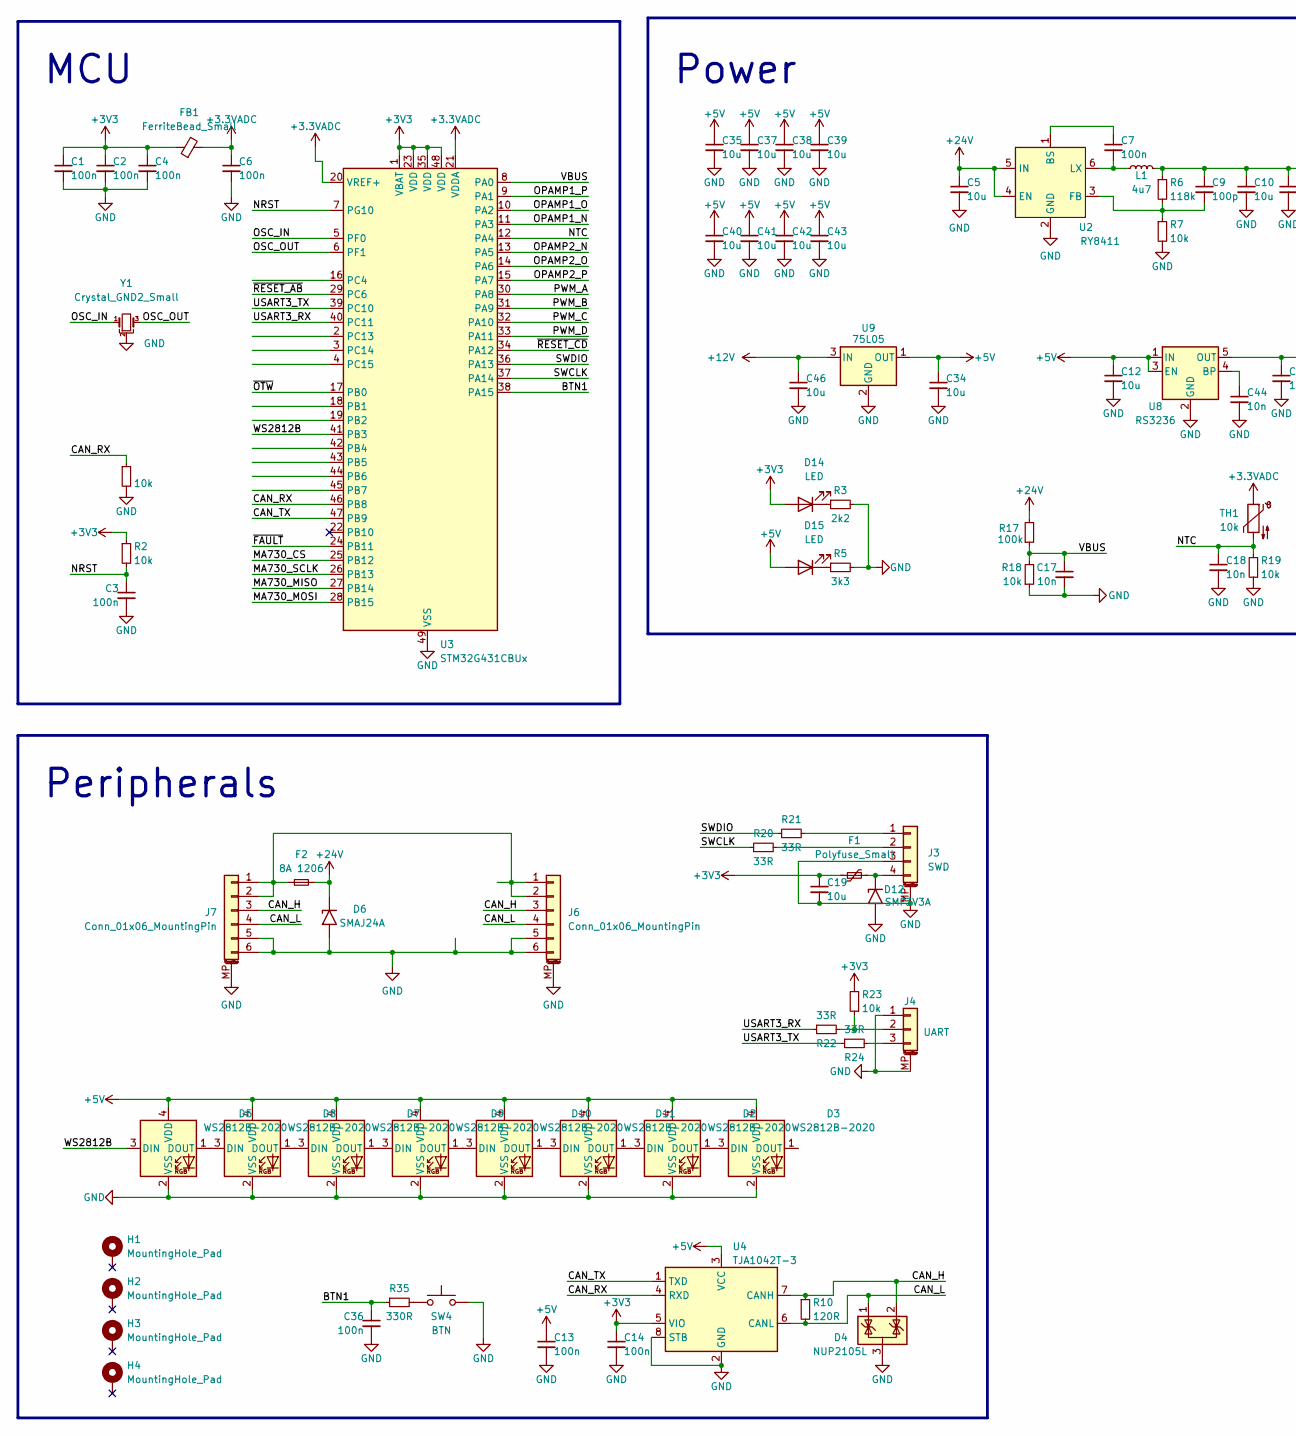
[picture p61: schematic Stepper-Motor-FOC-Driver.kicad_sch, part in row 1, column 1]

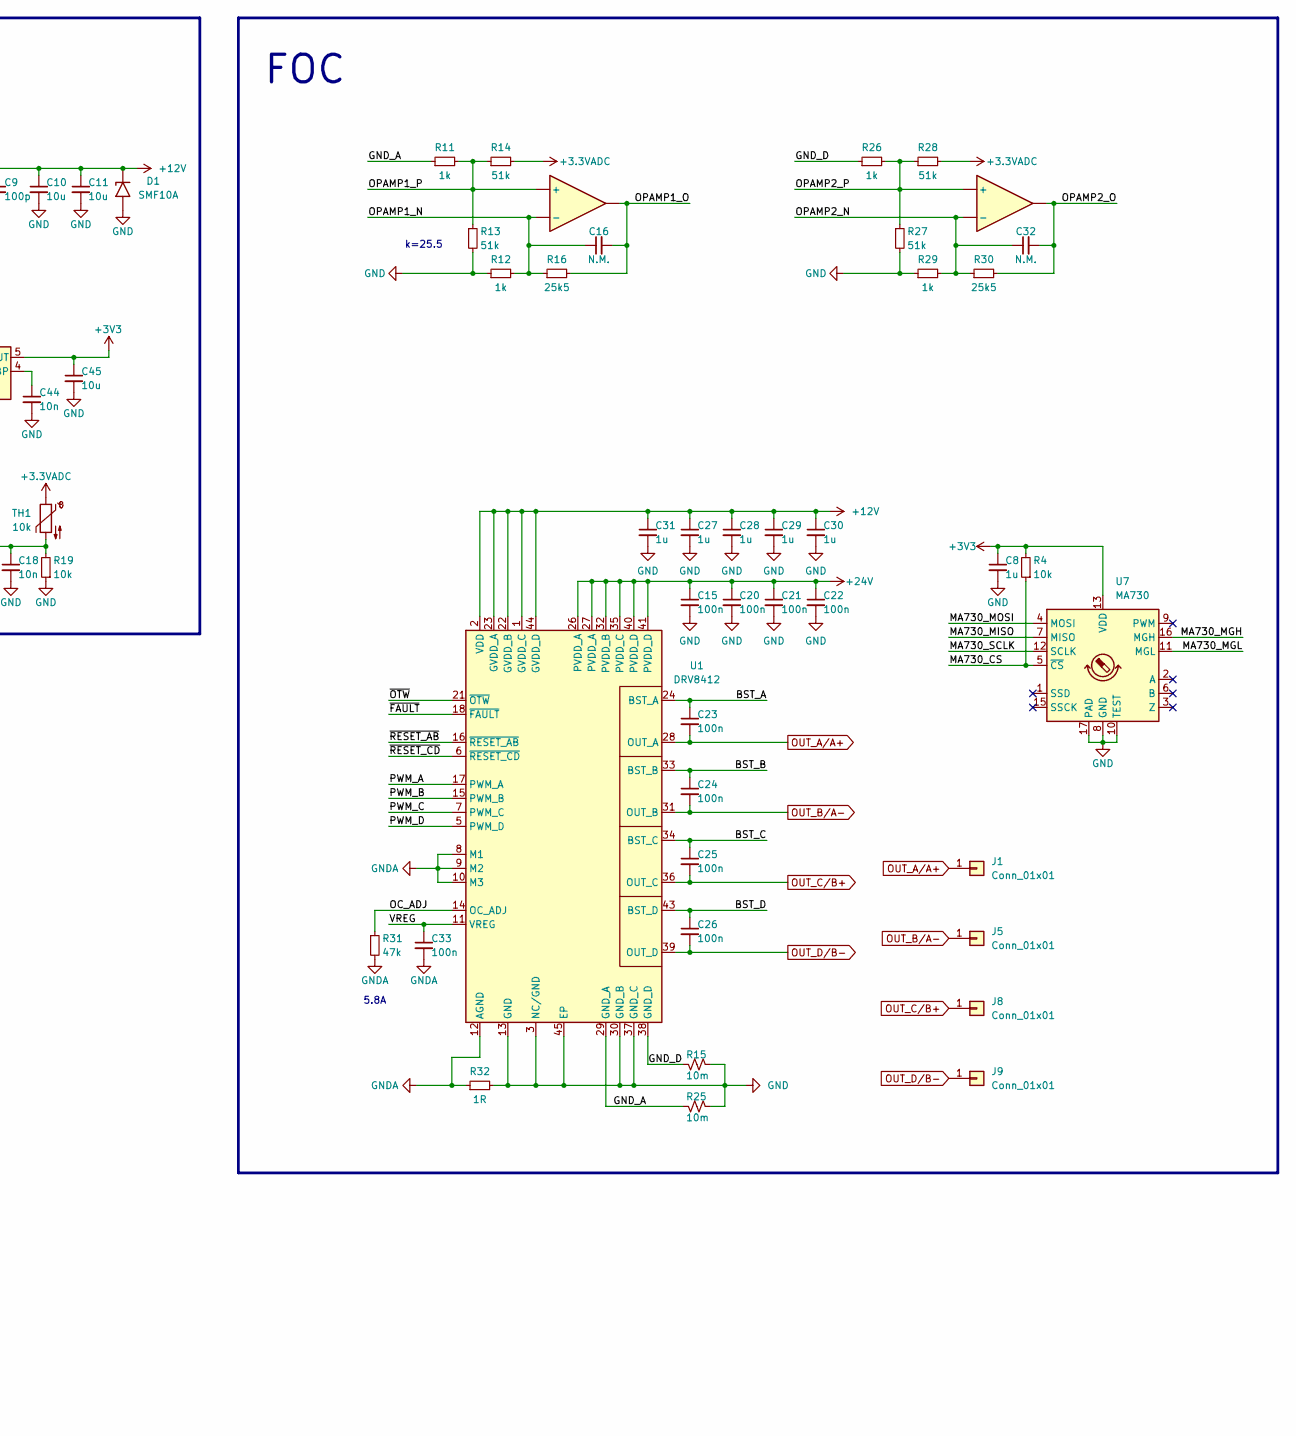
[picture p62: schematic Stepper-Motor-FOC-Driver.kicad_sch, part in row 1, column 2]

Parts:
C1, C2, C3, C4, C6, C7, C13, C14, C15, C20, C21, C22, C23, C24, C25, C26, C33, C36: 100n; C_0603_1608Metric
C5, C10, C11: 10u; C_1206_3216Metric
C8, C27, C28, C29, C30, C31: 1u; C_0603_1608Metric
C9: 100p; C_0603_1608Metric
C12, C19, C34, C35, C37, C38, C39, C40, C41, C42, C43, C45, C46: 10u; C_0603_1608Metric
C16, C32: N.M.; C_0603_1608Metric
C17, C18, C44: 10n; C_0603_1608Metric
D1: SMF10A; D_SMF
D2, D3, D5, D7, D8, D9, D10, D11: WS2812B-2020; LED_WS2812B-2020_PLCC4_2.0x2.0mm
D4: NUP2105L; SOT-23
D6: SMAJ24A; D_SMA
D12: SMF3V3A; D_SMF
D14, D15: LED; LED_0603_1608Metric
F1: Polyfuse_Small; Fuse_1206_3216Metric
F2: 8A 1206; Fuse_1206_3216Metric
FB1: FerriteBead_Small; L_0603_1608Metric
H1, H2, H3, H4: MountingHole_Pad; MountingHole_3.2mm_M3_DIN965_Pad
J1, J5, J8, J9: Conn_01x01; TestPoint_Pad_3.0x3.0mm
J3: SWD; Molex_PicoBlade_53047-0410_1x04_P1.25mm_Vertical
J4: UART; JST_GH_SM03B-GHS-TB_1x03-1MP_P1.25mm_Horizontal
J6, J7: Conn_01x06_MountingPin; JST_PH_S6B-PH-K_1x06_P2.00mm_Horizontal
L1: 4u7; L_Sunlord_MWSA0402S
R1, R2, R4, R7, R18, R19, R23: 10k; R_0603_1608Metric
R3: 2k2; R_0603_1608Metric
R5: 3k3; R_0603_1608Metric
R6: 118k; R_0603_1608Metric
R10: 120R; R_0603_1608Metric
R11, R12, R26, R29: 1k; R_0603_1608Metric
R13, R14, R27, R28: 51k; R_0603_1608Metric
R15, R25: 10m; R_1206_3216Metric
R16, R30: 25k5; R_0603_1608Metric
R17: 100k; R_0603_1608Metric
R20, R21, R22, R24: 33R; R_0603_1608Metric
R31: 47k; R_0603_1608Metric
R32: 1R; R_0603_1608Metric
R35: 330R; R_0603_1608Metric
SW4: BTN; SW_SPST_PTS810
TH1: 10k; TestPoint_2Pads_Pitch2.54mm_Drill0.8mm
U1: DRV8412; HTSSOP-44-1EP_6.1x14mm_P0.635mm_EP5.2x14mm_Mask4.31x8.26mm
U2: RY8411; SOT-23-6
U3: STM32G431CBUx; QFN-48-1EP_7x7mm_P0.5mm_EP5.6x5.6mm
U4: TJA1042T-3; SOIC-8_3.9x4.9mm_P1.27mm
U5, U6: type="X" model="OPAMP" lib=""
U7: MA730; QFN-16-1EP_3x3mm_P0.5mm_EP1.75x1.75mm
U8: RS3236; SOT-23-5
U9: 75L05; SOT-89-3
Y1: Crystal_GND2_Small; Resonator_SMD_Murata_CSTxExxV-3Pin_3.0x1.1mm

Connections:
+3.3VADC: C6.1, FB1.2, R14.2, R28.2, TH1.1, U3.20 (VREF+), U3.21 (VDDA)
+3V3: C1.1, C2.1, C4.1, C8.1, C14.1, C19.1, C45.1, D14.2 (A), F1.1, FB1.1, R2.1, R4.2, R23.2, U3.1 (VBAT), U3.23 (VDD), U3.35 (VDD), U3.48 (VDD), U4.5 (VIO), U7.13 (VDD), U8.5 (OUT)
+5V: C12.1, C13.1, C34.1, C35.1, C37.1, C38.1, C39.1, C40.1, C41.1, C42.1, C43.1, D2.4 (VDD), D3.4 (VDD), D5.4 (VDD), D7.4 (VDD), D8.4 (VDD), D9.4 (VDD), D10.4 (VDD), D11.4 (VDD), D15.2 (A), U4.3 (VCC), U8.1 (IN), U8.3 (EN), U9.1 (OUT)
+12V: C9.1, C10.1, C11.1, C27.1, C28.1, C29.1, C30.1, C31.1, C46.1, D1.1 (A1), L1.2, R6.1, U1.1 (GVDD_C), U1.2 (VDD), U1.22 (GVDD_B), U1.23 (GVDD_A), U1.44 (GVDD_D), U9.3 (IN)
+24V: C5.1, C15.1, C20.1, C21.1, C22.1, D6.1 (A1), F2.2, R17.2, U1.26 (PVDD_A), U1.27 (PVDD_A), U1.32 (PVDD_B), U1.35 (PVDD_C), U1.40 (PVDD_D), U1.41 (PVDD_D), U2.4 (EN), U2.5 (IN)
/BST_A: C23.1, U1.24 (BST_A)
/BST_B: C24.1, U1.33 (BST_B)
/BST_C: C25.1, U1.34 (BST_C)
/BST_D: C26.1, U1.43 (BST_D)
/BTN1: C36.1, R35.1, U3.38 (PA15)
/CAN_H: D4.2 (K), J6.3, J7.3, R10.1, U4.7 (CANH)
/CAN_L: D4.1 (K), J6.4, J7.4, R10.2, U4.6 (CANL)
/CAN_RX: R1.1, U3.46 (PB8), U4.4 (RXD)
/CAN_TX: U3.47 (PB9), U4.1 (TXD)
/GND_A: R11.1, R25.2, U1.29 (GND_A)
/GND_D: R15.2, R26.1, U1.38 (GND_D)
/MA730_CS: R4.1, U3.25 (PB12), U7.5 (~CS)
/MA730_MGH: U7.16 (MGH)
/MA730_MGL: U7.11 (MGL)
/MA730_MISO: U3.27 (PB14), U7.7 (MISO)
/MA730_MOSI: U3.28 (PB15), U7.4 (MOSI)
/MA730_SCLK: U3.26 (PB13), U7.12 (SCLK)
/NRST: C3.1, R2.2, U3.7 (PG10)
/NTC: C18.1, R19.2, TH1.2, U3.12 (PA4)
/OC_ADJ: R31.1, U1.14 (OC_ADJ)
/OPAMP1_N: C16.1, R12.2, R16.1, U3.11 (PA3), U5.
/OPAMP1_O: C16.2, R16.2, U3.10 (PA2), U5.
/OPAMP1_P: R11.2, R13.1, R14.1, U3.9 (PA1), U5.
/OPAMP2_N: C32.1, R29.2, R30.1, U3.13 (PA5), U6.
/OPAMP2_O: C32.2, R30.2, U3.14 (PA6), U6.
/OPAMP2_P: R26.2, R27.1, R28.1, U3.15 (PA7), U6.
/OSC_IN: U3.5 (PF0), Y1.1
/OSC_OUT: U3.6 (PF1), Y1.3
/PWM_A: U1.17 (PWM_A), U3.30 (PA8)
/PWM_B: U1.15 (PWM_B), U3.31 (PA9)
/PWM_C: U1.7 (PWM_C), U3.32 (PA10)
/PWM_D: U1.5 (PWM_D), U3.33 (PA11)
/SWCLK: R20.1, U3.37 (PA14)
/SWDIO: R21.1, U3.36 (PA13)
/USART3_RX: R22.1, U3.40 (PC11)
/USART3_TX: R24.1, U3.39 (PC10)
/VBUS: C17.1, R17.1, R18.2, U3.8 (PA0)
/VREG: C33.1, U1.11 (VREG)
/WS2812B: D5.3 (DIN), U3.41 (PB3)
/~FAULT: U1.18 (~FAULT), U3.24 (PB11)
/~OTW: U1.21 (~OTW), U3.17 (PB0)
/~RESET_AB: U1.16 (~RESET_AB), U3.29 (PC6)
/~RESET_CD: U1.6 (~RESET_CD), U3.34 (PA12)
GND: C1.2, C2.2, C3.2, C4.2, C5.2, C6.2, C8.2, C10.2, C11.2, C12.2, C13.2, C14.2, C15.2, C17.2, C18.2, C19.2, C20.2, C21.2, C22.2, C27.2, C28.2, C29.2, C30.2, C31.2, C34.2, C35.2, C36.2, C37.2, C38.2, C39.2, C40.2, C41.2, C42.2, C43.2, C44.2, C45.2, C46.2, D1.2 (A2), D2.2 (VSS), D3.2 (VSS), D4.3 (A), D5.2 (VSS), D6.2 (A2), D7.2 (VSS), D8.2 (VSS), D9.2 (VSS), D10.2 (VSS), D11.2 (VSS), D12.2 (A2), J3.3, J3.MP (MountPin), J4.1, J4.MP (MountPin), J6.5, J6.6, J6.MP (MountPin), J7.5, J7.6, J7.MP (MountPin), R1.2, R3.2, R5.2, R7.2, R12.1, R13.2, R15.1, R18.1, R19.1, R25.1, R27.2, R29.1, R32.2, SW4.2, U1.3 (NC/GND), U1.4 (NC/GND), U1.13 (GND), U1.19 (NC/GND), U1.20 (NC/GND), U1.25 (NC/GND), U1.30 (GND_B), U1.37 (GND_C), U1.42 (NC/GND), U1.45 (EP), U2.2 (GND), U3.49 (VSS), U4.2 (GND), U4.8 (STB), U7.8 (GND), U7.10 (TEST), U7.17 (PAD), U8.2 (GND), U9.2 (GND), Y1.2
GNDA: C33.2, R31.2, R32.1, U1.8 (M1), U1.9 (M2), U1.10 (M3), U1.12 (AGND)
unnamed: D2.1 (DOUT), D3.3 (DIN)
unnamed: D5.1 (DOUT), D8.3 (DIN)
unnamed: D7.3 (DIN), D8.1 (DOUT)
unnamed: D7.1 (DOUT), D9.3 (DIN)
unnamed: D9.1 (DOUT), D10.3 (DIN)
unnamed: D10.1 (DOUT), D11.3 (DIN)
unnamed: D2.3 (DIN), D11.1 (DOUT)
unnamed: D12.1 (A1), F1.2, J3.4
unnamed: D14.1 (K), R3.1
unnamed: D15.1 (K), R5.1
unnamed: J3.1, R21.2
unnamed: J3.2, R20.2
unnamed: J4.2, R22.2, R23.1
unnamed: J4.3, R24.2
unnamed: F2.1, J6.1, J6.2, J7.1, J7.2
unnamed: R35.2, SW4.1
unnamed: C7.1, U2.1 (BS)
unnamed: C9.2, R6.2, R7.1, U2.3 (FB)
unnamed: C7.2, L1.1, U2.6 (LX)
unnamed: C44.1, U8.4 (BP)
OUT_A/A+: C23.2, J1.1, U1.28 (OUT_A)
OUT_B/A-: C24.2, J5.1, U1.31 (OUT_B)
OUT_C/B+: C25.2, J8.1, U1.36 (OUT_C)
OUT_D/B-: C26.2, J9.1, U1.39 (OUT_D)

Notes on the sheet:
5.8A
Peripherals
FOC
MCU
Power
k=25.5

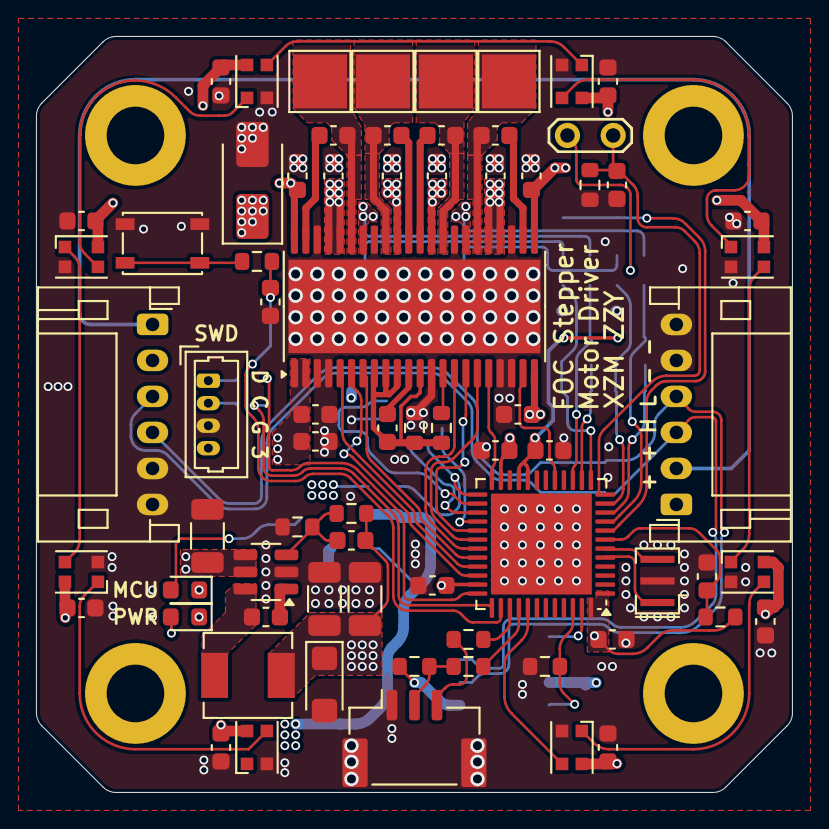
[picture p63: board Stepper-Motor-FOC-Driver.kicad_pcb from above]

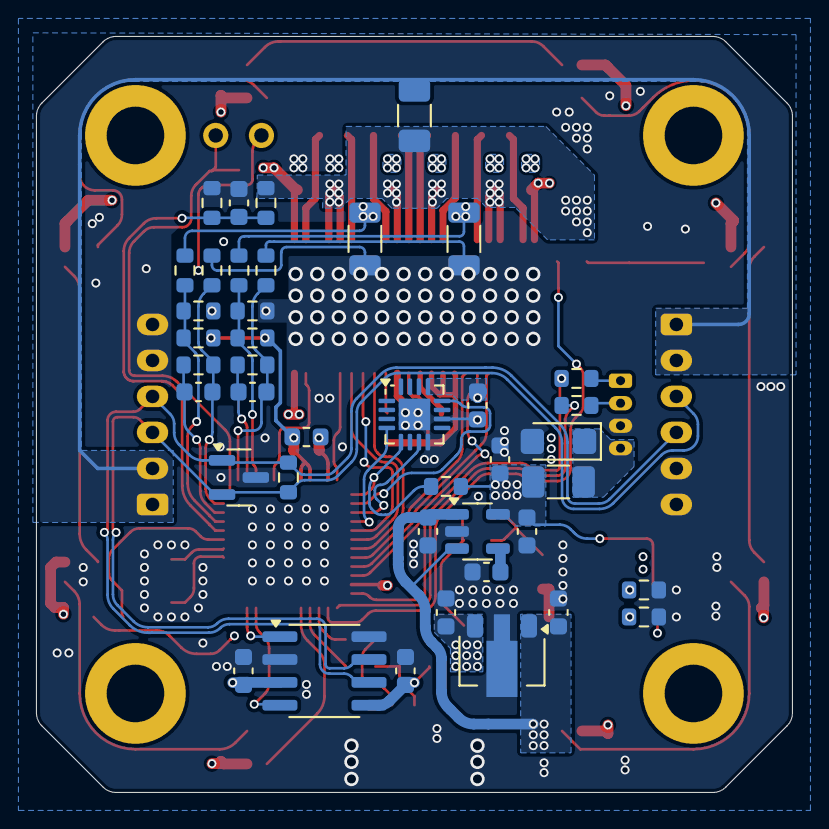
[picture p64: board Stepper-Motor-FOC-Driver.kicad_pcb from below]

Board: 4 copper layers, 42.0 x 42.0 mm, 117 parts (41 on the bottom side), 72 nets.

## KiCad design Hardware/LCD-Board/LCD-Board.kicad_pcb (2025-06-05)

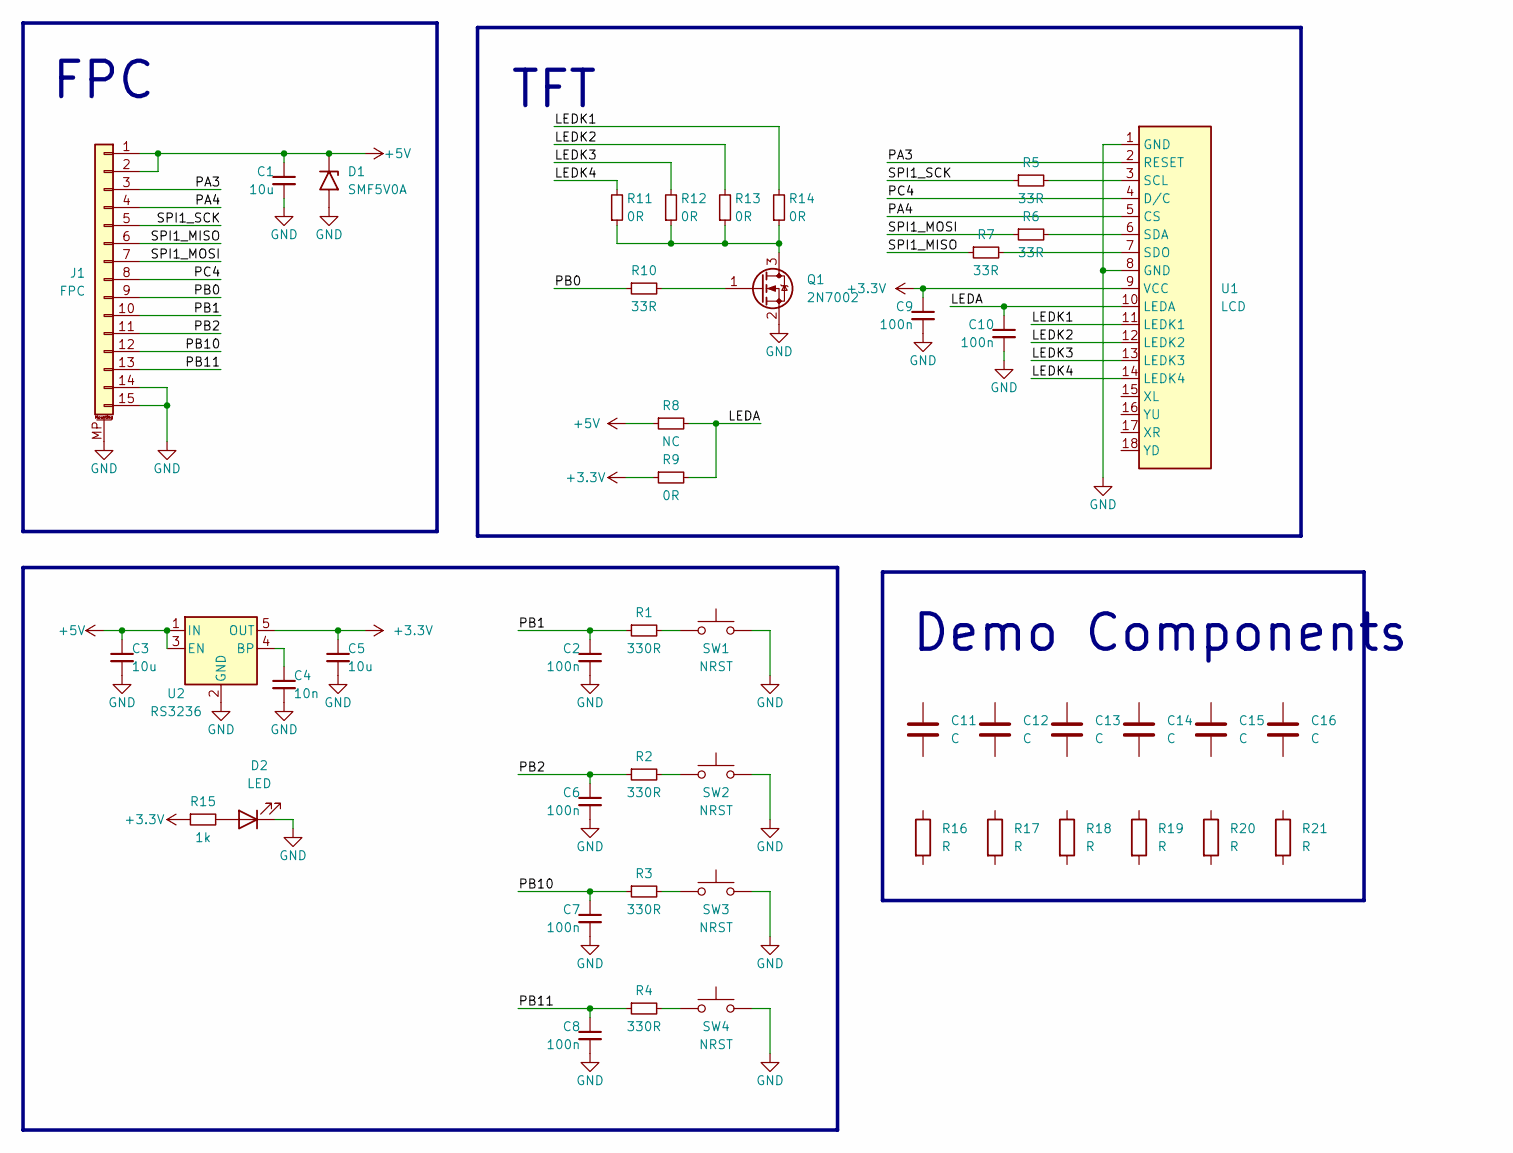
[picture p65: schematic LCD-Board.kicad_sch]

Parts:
C1, C3, C5: 10u; C_0603_1608Metric
C2, C6, C7, C8, C9, C10: 100n; C_0603_1608Metric
C4: 10n; C_0603_1608Metric
C11, C12, C13, C14, C15, C16: C; C_0805_2012Metric
D1: SMF5V0A; D_SMF
D2: LED; LED_0603_1608Metric
J1: FPC; TE_1-84952-5_1x15-1MP_P1.0mm_Horizontal
Q1: 2N7002; SOT-23
R1, R2, R3, R4: 330R; R_0603_1608Metric
R5, R6, R7, R10: 33R; R_0603_1608Metric
R8: NC; R_0603_1608Metric
R9, R11, R12, R13, R14: 0R; R_0603_1608Metric
R15: 1k; R_0603_1608Metric
R16, R17, R18, R19, R20, R21: R; R_0805_2012Metric
SW1, SW2, SW3, SW4: NRST; SW_SPST_PTS810
U1: LCD; Display_LCD_TFT_ST7789
U2: RS3236; SOT-23-5

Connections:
+3.3V: C5.1, C9.1, R9.1, R15.1, U1.9 (VCC), U2.5 (OUT)
+5V: C1.1, C3.1, D1.1 (A1), J1.1, J1.2, R8.1, U2.1 (IN), U2.3 (EN)
/LEDA: C10.1, R8.2, R9.2, U1.10 (LEDA)
/LEDK1: R14.2, U1.11 (LEDK1)
/LEDK2: R13.2, U1.12 (LEDK2)
/LEDK3: R12.2, U1.13 (LEDK3)
/LEDK4: R11.2, U1.14 (LEDK4)
/PA3: J1.3, U1.2 (RESET)
/PA4: J1.4, U1.5 (CS)
/PB0: J1.9, R10.1
/PB1: C2.1, J1.10, R1.1
/PB2: C6.1, J1.11, R2.1
/PB10: C7.1, J1.12, R3.1
/PB11: C8.1, J1.13, R4.1
/PC4: J1.8, U1.4 (D/C)
/SPI1_MISO: J1.6, R7.1
/SPI1_MOSI: J1.7, R6.1
/SPI1_SCK: J1.5, R5.1
GND: C1.2, C2.2, C3.2, C4.2, C5.2, C6.2, C7.2, C8.2, C9.2, C10.2, D1.2 (A2), D2.1 (K), J1.14, J1.15, J1.MP (MountPin), Q1.2 (S), SW1.2, SW2.2, SW3.2, SW4.2, U1.1 (GND), U1.8 (GND), U2.2 (GND)
unnamed: D2.2 (A), R15.2
unnamed: Q1.3 (D), R11.1, R12.1, R13.1, R14.1
unnamed: Q1.1 (G), R10.2
unnamed: R1.2, SW1.1
unnamed: R2.2, SW2.1
unnamed: R3.2, SW3.1
unnamed: R4.2, SW4.1
unnamed: R5.2, U1.3 (SCL)
unnamed: R6.2, U1.6 (SDA)
unnamed: R7.2, U1.7 (SDO)
unnamed: C4.1, U2.4 (BP)

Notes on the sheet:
TFT
Demo Components
FPC

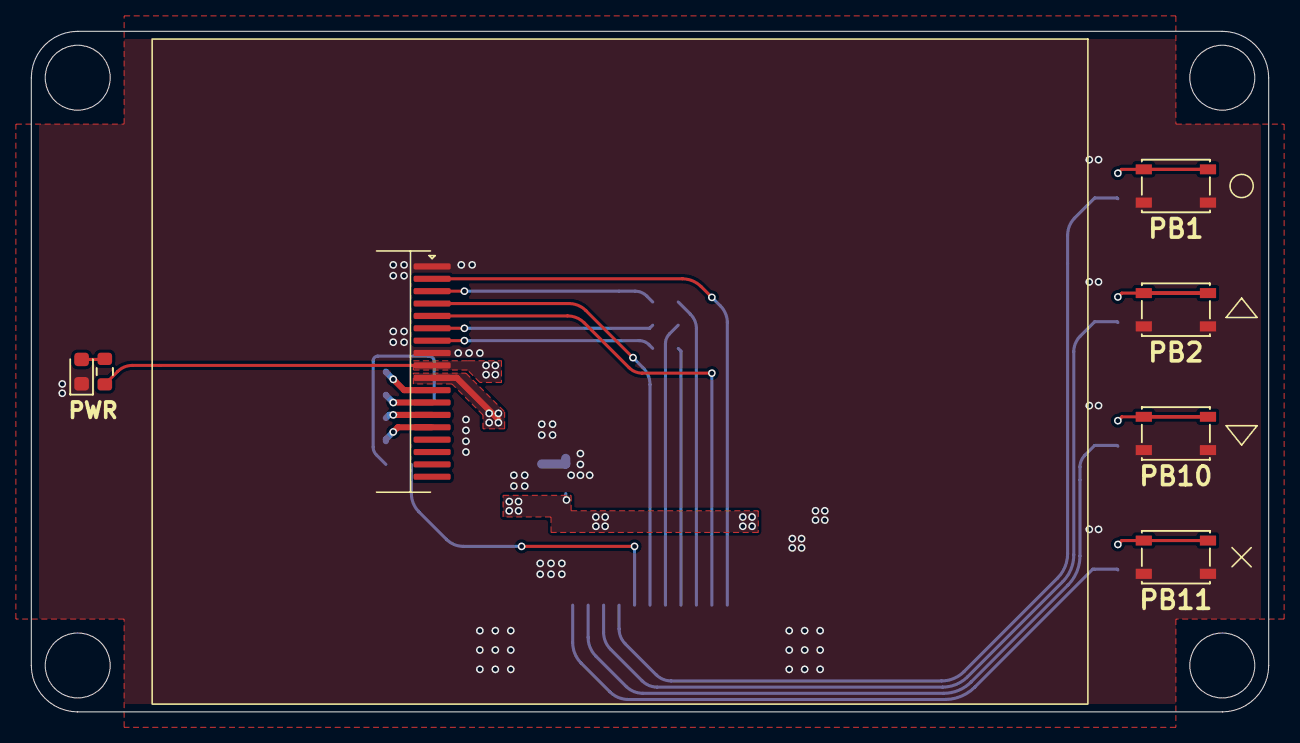
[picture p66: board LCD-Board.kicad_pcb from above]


Board: 2 copper layers, 80.0 x 44.0 mm, 47 parts (40 on the bottom side), 30 nets.

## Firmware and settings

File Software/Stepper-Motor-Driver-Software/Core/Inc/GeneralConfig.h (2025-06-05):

#ifndef __GENERAL_CONFIG_H
#define __GENERAL_CONFIG_H

#include "stdint.h"

/* 外设配置 */
#define CURRENT_LOOP_FREQ           42500       // 电流环频率, 单位 Hz
#define CCR                         1000        // Counter Period

#define CAN_ID                      3           // 自己的 CAN ID, 1~8

#define FDCANMANAGER_FILTER_ID      0x100       // FDCAN 接受的 ID
#define FDCANMANAGER_FILTER_ID_MASK 0x7F0       // FDCAN 接受的 ID 掩码

/* 物理参数 */
#define AB_PHASE_SWAP               0           // 1 为交叉接法, 0 为正常接法
#define POLE_PAIRS                  50          // 极对数, 1.8° 步进电机是 50 对
#define PHASE_RESISTANCE            2.11453f    // 相电阻, 2.11453Ω
#define PHASE_INDUCTANCE            2.00f       // 相电感, 2.00mH
#define KV                          800.0f      // 37.5 RPM/V

/* 校准数据 */
#if (CAN_ID == 1)
#define VBUS_GAIN                   0.008946261f    // 电压采样增益
#define IALPHA_BIAS                 2037.52173f     // 电流采样偏置
#define IALPHA_GAIN                 -0.002982521f   // 电流采样增益
#define IBETA_BIAS                  2031.25757f     // 电流采样偏置
#define IBETA_GAIN                  0.003155451f    // 电流采样增益
#elif (CAN_ID == 2)
#define VBUS_GAIN                   0.008946261f    // 电压采样增益
#define IALPHA_BIAS                 2039.27039f     // 电流采样偏置
#define IALPHA_GAIN                 -0.002781669f   // 电流采样增益
#define IBETA_BIAS                  2020.38947f     // 电流采样偏置
#define IBETA_GAIN                  0.0027568069f   // 电流采样增益
#elif (CAN_ID == 3)
// 未校准
#define VBUS_GAIN                   0.008946261f    // 电压采样增益
#define IALPHA_BIAS                 2039.27039f     // 电流采样偏置
#define IALPHA_GAIN                 -0.002781669f   // 电流采样增益
#define IBETA_BIAS                  2020.38947f     // 电流采样偏置
#define IBETA_GAIN                  0.0027568069f   // 电流采样增益
#endif

/* 控制 */
#define CALIBRATE_ENCODER           0           // 是否校准编码器

#define DEFAULT_TOURQUE_LIMIT       1.5f        // 默认扭矩限制, 单位 A

#if (CAN_ID == 1 || CAN_ID == 2)
#define DEFAULT_VELOCITY_LIMIT      200000      // 默认速度限制, 轴角速度定点数 / s
#else
#define DEFAULT_VELOCITY_LIMIT      10000       // 默认速度限制, 轴角速度定点数 / s
#endif

#define OPEN_LOOP_ROTATE_SPEED      64          // 开环转速, 每次调用电流环增加的角度, 定点数

#if (CAN_ID == 1 || CAN_ID == 2)
#define OPENLOOP_DRAG_VOLTAGE       3.0f        // 开环拖动电压, 单位 V
#else
#define OPENLOOP_DRAG_VOLTAGE       2.0f        // 开环拖动电压, 单位 V
#endif

#define ALINE_VOLTAGE               8.0f       // 对齐电角度的电压, 单位 V

#define UNDER_VOLTAGE_THRESHOLD     16.0f       // 电压低于此值会触发 underOverVoltageError
#define OVER_VOLTAGE_THRESHOLD      30.0f       // 电压高于此值会触发 underOverVoltageError
#define OVER_TEMPERATURE_THRESHOLD  80.0f       // 温度高于此值会触发 overTemperatureError
#define OVER_CURRENT_THRESHOLD      8.0f        // 电流大于此值会触发 overCurrentError

#define ERROR_TRIGGER_TRESHOLD_TIME CURRENT_LOOP_FREQ   // 多少个 tick 会触发错误, 不同类型的错误触发 Counter 加速度可以不一样
#define UNDER_OVER_VOLTAGE_TRIGGER_SPEED    20
#define UNDER_OVER_VOLTAGE_UNTRIGGER_SPEED  1
#define OVER_TEMPERATURE_TRIGGER_SPEED      1
#define OVER_TEMPERATURE_UNTRIGGER_SPEED    1
#define OVER_CURRENT_TRIGGER_SPEED          20
#define OVER_CURRENT_UNTRIGGER_SPEED        1

#define MA732_USE_KALMAN_FILTER     0           // 是否使用卡尔曼滤波器 0 使用 LPF, 1 使用卡尔曼滤波器

#define MUSIC_STRENGTH              OPENLOOP_DRAG_VOLTAGE  // 音乐模式的电压


/* 常数和基本函数 */
#define PI 3.1415926f
#define TWO_PI 6.2831853f

#define CLAMP(x, min, max) ((x) > (max) ? (max) : ((x) < (min) ? (min) : (x)))

#define FABS(x) ((x) > 0 ? (x) : -(x))
#define FMOD(x, y) ((x) - (int32_t)((x) / (y)) * (y))
#endif

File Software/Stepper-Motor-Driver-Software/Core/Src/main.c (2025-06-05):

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
/* Includes ------------------------------------------------------------------*/
#include "main.h"
#include "adc.h"
#include "cordic.h"
#include "dma.h"
#include "fdcan.h"
#include "opamp.h"
#include "spi.h"
#include "tim.h"
#include "gpio.h"

/* USER CODE BEGIN Includes */
#include "fdcan.h"
#include "math.h"
#include "stdint.h"

#include "tick.h"
#include "ws2812.h"
#include "FOC.h"
#include "MA732.h"
#include "PositionalPID.h"
#include "IncrementalPID.h"
#include "Calibrator.h"
#include "ErrorHandler.h"
#include "InterBoard.h"
#include "LightEffect.h"
/* USER CODE END Includes */


/* USER CODE BEGIN PV */
uint8_t r = 0, g = 0, b = 0;
uint8_t WS2812_brightness = 30;
uint8_t signal1KHz = 0, signal500Hz = 0;

/* USER CODE END PV */

void SystemClock_Config(void);
/**
  * @brief  The application entry point.
  * @retval int
  */
int main(void)
{

  /* MCU Configuration--------------------------------------------------------*/

  /* Reset of all peripherals, Initializes the Flash interface and the Systick. */
  HAL_Init();

  /* Configure the system clock */
  SystemClock_Config();

  /* Initialize all configured peripherals */
  MX_GPIO_Init();
  MX_DMA_Init();
  MX_FDCAN1_Init();
  MX_OPAMP1_Init();
  MX_OPAMP2_Init();
  MX_SPI2_Init();
  MX_TIM1_Init();
  MX_ADC2_Init();
  MX_TIM2_Init();
  MX_TIM6_Init();
  MX_ADC1_Init();
  MX_CORDIC_Init();
  /* USER CODE BEGIN 2 */
  // FLASH_OBProgramInitTypeDef pOBInit;
  // HAL_FLASHEx_OBGetConfig(&pOBInit);
  // if (!((pOBInit.USERConfig & FLASH_OPTR_nSWBOOT0_Msk) == OB_BOOT0_FROM_OB &&
  //       (pOBInit.USERConfig & FLASH_OPTR_nBOOT0_Msk) == OB_nBOOT0_SET &&
  //       (pOBInit.USERConfig & FLASH_OPTR_NRST_MODE_Msk) == OB_NRST_MODE_GPIO &&
  //       (pOBInit.USERConfig & FLASH_OPTR_BOR_LEV_Msk) == OB_BOR_LEVEL_4 &&
  //       (pOBInit.USERConfig & FLASH_OPTR_nRST_STOP_Msk) == OB_STOP_RST &&
  //       (pOBInit.USERConfig & FLASH_OPTR_nRST_STDBY_Msk) == OB_STANDBY_RST &&
  //       (pOBInit.USERConfig & FLASH_OPTR_nRST_SHDW_Msk) == OB_SHUTDOWN_RST
  // )) {
  //     __disable_irq();
  //     HAL_FLASH_Unlock();
  //     HAL_FLASH_OB_Unlock();

  //     pOBInit.OptionType = OPTIONBYTE_USER;
  //     pOBInit.USERType = 0;
  //     pOBInit.USERConfig = 0;

  //     pOBInit.USERType |= OB_USER_nSWBOOT0;
  //     pOBInit.USERConfig |= OB_BOOT0_FROM_OB;
  //     pOBInit.USERType |= OB_USER_nBOOT0;
  //     pOBInit.USERConfig |= OB_nBOOT0_SET;
  //     pOBInit.USERType |= OB_USER_NRST_MODE;
  //     pOBInit.USERConfig |= OB_NRST_MODE_GPIO;
  //     pOBInit.USERType |= OB_USER_BOR_LEV;
  //     pOBInit.USERConfig |= OB_BOR_LEVEL_4;
  //     pOBInit.USERType |= OB_USER_nRST_STOP;
  //     pOBInit.USERConfig |= OB_STOP_RST;
  //     pOBInit.USERType |= OB_USER_nRST_STDBY;
  //     pOBInit.USERConfig |= OB_STANDBY_RST;
  //     pOBInit.USERType |= OB_USER_nRST_SHDW;
  //     pOBInit.USERConfig |= OB_SHUTDOWN_RST;
  //     pOBInit.USERType |= OB_USER_IRHEN;
  //     pOBInit.USERConfig |= OB_IRH_ENABLE;
  //     HAL_FLASHEx_OBProgram(&pOBInit);
  //     HAL_FLASH_OB_Launch();
  //     HAL_FLASH_OB_Lock();
  //     HAL_FLASH_Lock();
  //     __enable_irq();
  // }
  /* USER CODE END 2 */

  /* Infinite loop */
  /* USER CODE BEGIN WHILE */
  motorControlStatus.initializing = 1;
  // WS2812 初始�?
  Tick_Init();
  ErrorHandlerInit();
  WS2812_Init();

  MA732_Init(&hspi2);

  MotorControlInit();
  InterBoardInit();

  // ADC 运放 初始�?
  HAL_OPAMP_Start(&hopamp1);
  HAL_OPAMP_Start(&hopamp2);

  HAL_ADCEx_Calibration_Start(&hadc1, ADC_SINGLE_ENDED);
  HAL_ADCEx_Calibration_Start(&hadc2, ADC_SINGLE_ENDED);

  HAL_ADC_Start(&hadc2);
  extern uint32_t adcBuffer[2];
  HAL_ADCEx_MultiModeStart_DMA(&hadc1, adcBuffer, 2);

  disableFOC();
  // 这样做的目的是修改TIM1 Update Event 的相�?
  HAL_TIM_Base_Start_IT(&htim1);
  htim1.Instance->RCR = 1;
  HAL_TIM_PWM_Start(&htim1, TIM_CHANNEL_1);
  HAL_TIM_PWM_Start(&htim1, TIM_CHANNEL_2);
  HAL_TIM_PWM_Start(&htim1, TIM_CHANNEL_3);
  HAL_TIM_PWM_Start(&htim1, TIM_CHANNEL_4);

  HAL_GPIO_WritePin(NRST_AB_GPIO_Port, NRST_AB_Pin, GPIO_PIN_SET);
  HAL_GPIO_WritePin(NRST_CD_GPIO_Port, NRST_CD_Pin, GPIO_PIN_SET);  

  HAL_Delay(50);
  #if (CAN_ID == 2)
  HAL_Delay(600);
  #endif
  #if (CAN_ID == 3)
  HAL_Delay(1200);
  #endif
  alineMotor();
  // calibrateCurrentSensor();
  // Never reach here
  #if (CALIBRATE_ENCODER == 1)
  calibrateEncoder();
  // Never reach here
  #endif

  resetAndEnableFOC();
  motorControlStatus.initializing = 0;
  while (1)
  {
    /* USER CODE END WHILE */

    /* USER CODE BEGIN 3 */
    if(motorControlStatus.triggerReset)
    {
      // 尝试手动触发复位, 清除故障标志
      motorControlStatus.triggerReset = 0;
      resetAndEnableFOC();
      ErrorHandlerClearErrorStatus();
    }

    if(ErrorHandlerCheckIfAnyError())
    {
      lightEffect_UniColor(255, 25, 25);
    }
    else
    {
      /*r = sin(vTick / 1000.0) * WS2812_brightness + WS2812_brightness;
      g = sin(vTick / 1000.0 + 2 * 3.14159 / 3) * WS2812_brightness + WS2812_brightness;
      b = sin(vTick / 1000.0 + 4 * 3.14159 / 3) * WS2812_brightness + WS2812_brightness;
      for(int i = 0; i < 8; i++)
      { 
        blink(i, r, g, b);
      }   */ 
      lightEffect_Angle(1, 255, 60, 60, 60);
      lightEffect_Rainbow(1000, 255);

    }

    #if (CAN_ID == 3)
    // motorStalled 复用为 MicroSwitch 是否被触发
    motorErrorStatus.motorStalled = 1 - HAL_GPIO_ReadPin(MicroSwitch_GPIO_Port, MicroSwitch_Pin);
    #endif

    signal500Hz += 1;
    if(signal500Hz == 2)
    {
      InterBoardTransmitFeedback();
      signal500Hz = 0;
    }
    
    
    // 保证 1KHz 的控制周期
    while(signal1KHz == 0);
    signal1KHz = 0;
  }
  /* USER CODE END 3 */
}

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


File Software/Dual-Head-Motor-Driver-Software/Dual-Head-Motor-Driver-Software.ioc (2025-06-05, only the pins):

Mcu.UserName=STM32G431CBUx
PA0.GPIO_Label=GPIO1
PA0.Signal=GPIO_Input
PA1.Signal=OPAMP1_VINP
PA10.Signal=S_TIM1_CH3
PA11.Signal=FDCAN1_RX
PA12.Signal=FDCAN1_TX
PA13.Signal=SYS_JTMS-SWDIO
PA14.Signal=SYS_JTCK-SWCLK
PA15.Signal=S_TIM2_CH1
PA2.Signal=SharedAnalog_PA2
PA3.Signal=OPAMP1_VINM0
PA4.GPIO_Label=MICRO_SW
PA4.Signal=GPIO_Input
PA5.Signal=OPAMP2_VINM0
PA6.Signal=SharedAnalog_PA6
PA7.Signal=OPAMP2_VINP
PA8.Signal=S_TIM1_CH1
PA9.Signal=S_TIM1_CH2
PB0.Signal=OPAMP3_VINP
PB1.Signal=SharedAnalog_PB1
PB11.GPIO_Label=VBUS_SENSE
PB11.Signal=SharedAnalog_PB11
PB12.GPIO_Label=GPIO2
PB12.Signal=GPIO_Input
PB13.GPIO_Label=VALVE_1
PB13.Signal=GPIO_Output
PB2.Signal=OPAMP3_VINM0
PB3.Signal=S_TIM2_CH2
PB4.GPIO_Label=M2_nFAULT
PB4.Signal=GPIO_Input
PB5.GPIO_Label=M3_nFAULT
PB5.Signal=GPIO_Input
PB6.Signal=S_TIM4_CH1
PB7.Signal=S_TIM4_CH2
PB8-BOOT0.Signal=S_TIM4_CH3
PB9.Signal=S_TIM4_CH4
PC10.Signal=TIM8_CH1N
PC11.Signal=TIM8_CH2N
PC13.GPIO_Label=M1_nFAULT
PC13.Signal=GPIO_Input
PC14-OSC32_IN.GPIO_Label=VALVE_2
PC14-OSC32_IN.Signal=GPIO_Output
PC15-OSC32_OUT.GPIO_Label=GPIO3
PC15-OSC32_OUT.Signal=GPIO_Input
PC6.Signal=S_TIM3_CH1
PF0-OSC_IN.Signal=RCC_OSC_IN
PF1-OSC_OUT.Signal=RCC_OSC_OUT

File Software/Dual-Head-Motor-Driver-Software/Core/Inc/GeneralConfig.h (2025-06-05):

/**
 * @file GeneralConfig.h
 * @author Baoqi (zzhongas@connect.ust.hk)
 *
 * @copyright Copyright (c) 2025
 */

#pragma once
#include "stdint.h"

/* 外设配置 */
// PWM 频率: 170 / 2 / 4000 = 21.25 KHz
#define CURRENT_LOOP_FREQ           21250       // 电流环频率, 单位 Hz
#define CCR                         4000        // Counter Period

#define CAN_ID                      3           // 自己的 CAN ID, 1~8

#define FDCANMANAGER_FILTER_ID      0x100       // FDCAN 接受的 ID
#define FDCANMANAGER_FILTER_ID_MASK 0x7F0       // FDCAN 接受的 ID 掩码

/* 物理参数 */
#define POLE_PAIRS                  50          // 极对数, 1.8° 步进电机是 50 对
#define PHASE_RESISTANCE            2.11453f    // 相电阻, 2.11453Ω

#define KV_M1                       3.0f        // 电机 1 的速度常数, V/(rad/s)
#define KV_M2                       0.1f        // 电机 2 的速度常数, V/(rad/s)

#define ARM_LENGTH                  29.0f       // 摇臂长度, 单位 mm
#define WHEEL_RADIUS                7.5f       // 轮子半径, 单位 mm

/* 校准数据 */
#define VBUS_GAIN                   0.00492074f // 电压采样增益
#define IM1_BIAS                    0           // 电流采样偏置
#define IM1_GAIN                    1           // 电流采样增益
#define IM2_BIAS                    0           // 电流采样偏置
#define IM2_GAIN                    1           // 电流采样增益
#define IM3_BIAS                    0           // 电流采样偏置
#define IM3_GAIN                    1           // 电流采样增益


/* 控制 */
#define DEFAULT_TOURQUE_LIMIT_M1    1.5f        // 默认扭矩限制, 单位 A
#define DEFAULT_ACC_LIMIT_M1        5.0f        // 默认加速度限制, 轴角加速度 rad/s^2
#define DEFAULT_VELOCITY_LIMIT_M1   2.0f        // 默认速度限制, 轴角速度 rad/s
#define POSITIOIN_HOLD_VOLTAGE_M1   7.0f        // 位置保持电压, 单位 V

#define DEFAULT_TOURQUE_LIMIT_M2    1.5f        // 默认扭矩限制, 单位 A
#define DEFAULT_ACC_LIMIT_M2        2000.0f     // 默认加速度限制, 轴角加速度 rad/s^2
#define DEFAULT_VELOCITY_LIMIT_M2   100.0f      // 默认速度限制, 轴角速度 rad/s
#define POSITIOIN_HOLD_VOLTAGE_M2    2.0f       // 位置保持电压, 单位 V

#define OPEN_LOOP_ROTATE_SPEED_M1   1.0f        // 开环转速, 每次调用电流环增加的角度
#define OPEN_LOOP_ROTATE_SPEED_M2   2.0f        // 开环转速, 每次调用电流环增加的角度

#define UNDER_VOLTAGE_THRESHOLD     8.2f        // 电压低于此值会触发 underOverVoltageError
#define OVER_VOLTAGE_THRESHOLD      18.5f       // 电压高于此值会触发 underOverVoltageError
#define OVER_CURRENT_THRESHOLD      2.0f        // 电流大于此值会触发 overCurrentError

#define ERROR_TRIGGER_TRESHOLD_TIME CURRENT_LOOP_FREQ   // 多少个 tick 会触发错误, 不同类型的错误触发 Counter 加速度可以不一样
#define UNDER_OVER_VOLTAGE_TRIGGER_SPEED    20
#define UNDER_OVER_VOLTAGE_UNTRIGGER_SPEED  1
#define OVER_CURRENT_TRIGGER_SPEED          20
#define OVER_CURRENT_UNTRIGGER_SPEED        1


/* 常数和基本函数 */
#define PI 3.1415926f
#define TWO_PI 6.2831853f

#define CLAMP(x, min, max) ((x) > (max) ? (max) : ((x) < (min) ? (min) : (x)))

#define MIN(x, y) ((x) < (y) ? (x) : (y))
#define MAX(x, y) ((x) > (y) ? (x) : (y))
#define FABS(x) ((x) > 0 ? (x) : -(x))
#define FMOD(x, y) ((x) - (int32_t)((x) / (y)) * (y))

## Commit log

2025-06-05 Add Hardware File
    [1.54 TFT IPS - 12P - Flat Flush Mount.stp, 1.54 TFT IPS - Reverse Mount.stp, Dual-Head-Motor-Driver.kicad_pcb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]
2025-06-05 Add Mech/Software/Readme
    [0.15_7_7拉簧.SLDPRT, 0603_ComponentHolderType.SLDPRT, 17HS08-1004S.SLDPRT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]

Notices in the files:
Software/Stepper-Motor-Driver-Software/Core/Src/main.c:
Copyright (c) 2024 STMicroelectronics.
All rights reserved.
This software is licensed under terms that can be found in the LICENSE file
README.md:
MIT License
